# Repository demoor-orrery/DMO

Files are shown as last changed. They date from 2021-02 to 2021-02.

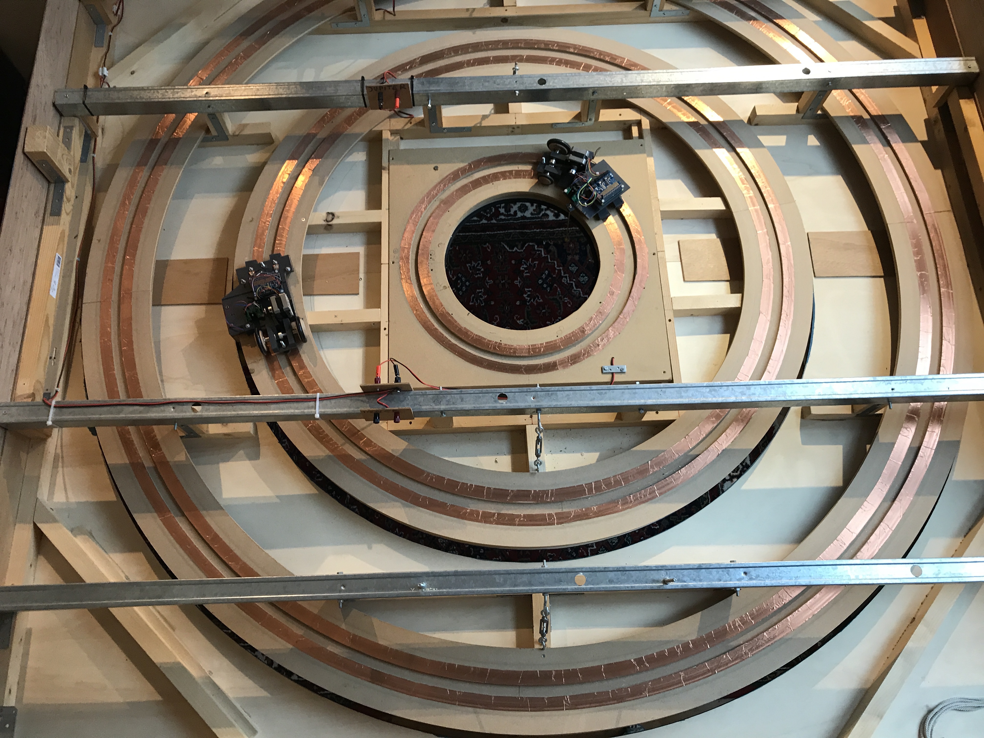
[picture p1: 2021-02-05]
pictures/DM005 frame overview without inner planets.JPG

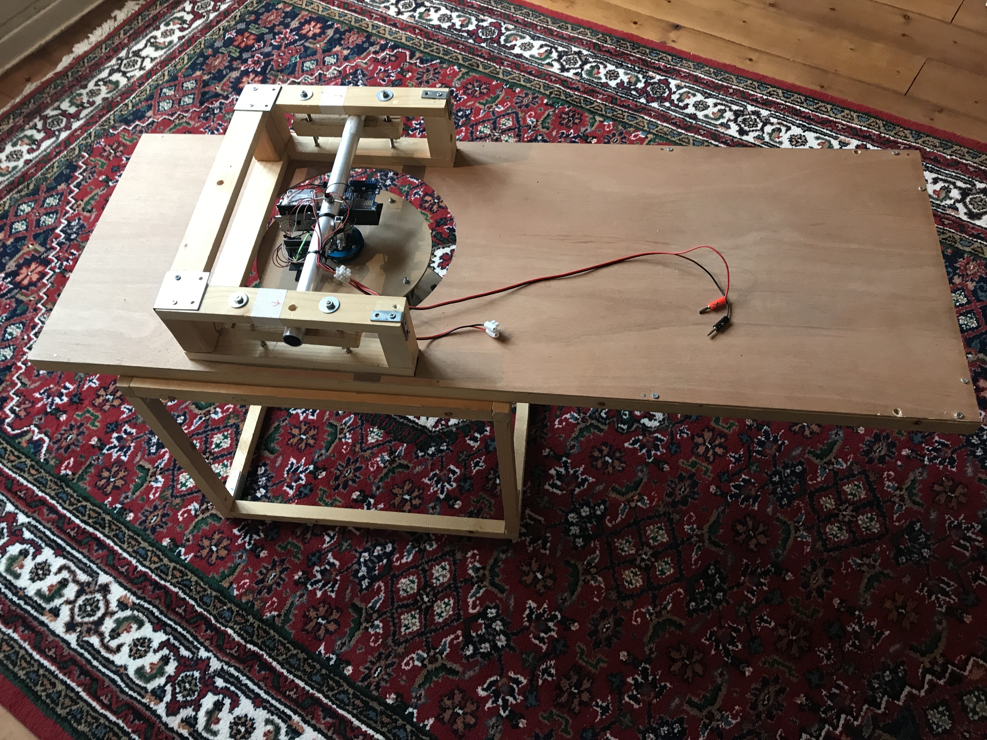
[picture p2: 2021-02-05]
pictures/DM007 inner system on floor.JPG

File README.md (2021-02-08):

# www.demoor-orrery.com/en

here all files are stored which will help to build your own planetrium

DMO.py <br>
the only file you need to run on your Pi

/documentation<br> 
please read them all before you start

/pictures<br>
all pictures used in documentation in full resolution for more details

/gerber file PCB<br>
files you need to print your own PCB board

/STL files for 3D <br>
all STL files for all components 

/webserver <br>
the adjusted JSOrrery software to run on your webserver for your DMO

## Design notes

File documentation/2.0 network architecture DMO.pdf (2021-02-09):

Tuesday, 9 February 2021

## 2.0 Network architecture DMO

2.1 Version control

Version 1.0 - 2 February 2021 - first version Version 1.1 - 9 February 2021 - typos fixed

2.2 Introduction

Each planet has its own computer (Raspberry Pi Zero W). A stepper motor (Nema
17) with accompanying driver (Adafruit Motor HAT) is connected so the planet can be exactly positioned. Initial positioning is done with reed-switches that react to magnets on the track.

The position of the planet is calculated on a website which is hosted on a webserver. Each planet can read the output via WiFi and calculate where its place is on the planet orbit for the entered date and then "drive" to it.

2.3 Architecture

webserver | the internet | DMO

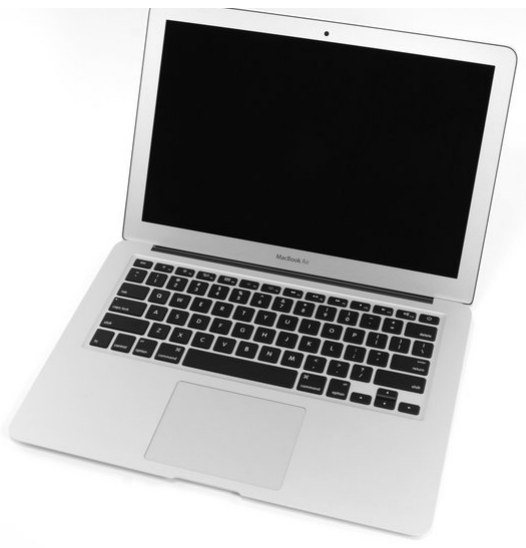
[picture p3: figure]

laptop, phone or tablet

1 | www.demoor-orrery.com/en

Tuesday, 9 February 2021
2.3.1 Webserver and software

The webserver can be any hosting-server, it is used to store the solar-systemsoftware. You can use any hosting-partner or set up one yourself in your network. As long as it runs the original JS Orrery software: http://mgvez.github.io/jsorrery/

Hosting it on an external server has the benefit you can operate the DMO outside your local premisses (anywhere in the world in fact).

The original JS Orrery software has been modified with adding a “save positions” button. What is basically does is sending out a string of degrees where the planets are on the entered date.

The string can be read at:

http://yourdomain.xxx/positions.txt

Example of possible output:

360185244155101132045097

The first three digits are for Mercury and so on (inside out until Pluto). The last three planets are not in the DMO but maybe in your DMO.

In our DMO Git account you will find the adjusted JS Orrery software you need to install on your webserver.

2.3.2 DMO

The DMO consist of 6 Raspberry Pi Zero W’s (RPI) which are all connected to the same local WiFi network. All planets (from Mercury to Saturn) “know” who they are and read their own part of the string for their position in their orbit.

2.3.3 Laptop, phone or tablet

With your terminal (doesn’t matter what it is as long as it runs a web-browser and supports Javascript) you can acces the webserver on your domain (http://yourdomain.xxx).

You enter the desired date, hit return and push “save positions”. The string is published and picked up by the relevant RPI’s. A RPI “knows” where it is via a reed switch which runs over a magnet, recalculates the degrees into number of steps and moves to the desired position.

2 | www.demoor-orrery.com/en

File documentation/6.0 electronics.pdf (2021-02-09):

Tuesday, 9 February 2021

## 6.0 Electronics

6.1 Version control

Version 1.0 - 2 February 2021 - first version Version 1.1 - 9 February 2021 - typos fixed

6.2 Introduction

This part of the documentation describes the electronics. That is the same for inner and outer planets. The basis consist of five parts: RPI, driver, stepper motor, power supply, reed switch

6.3 RPI

Not much to say here: you need a Raspberry Pi Zero W (or any other Pi with Wifi).

6.4 Driver

You need the Adafruit DC & Stepper Motor HAT for Raspberry Pi - Mini Kit. It comes along with a nice software library on which the DMO software is based.

6.5 Stepper motor

The NEMA17 is chosen for its availability, robustness and torque.

6.6 Power supply

The driver runs on 12V but the RPI on 5v, so the voltage must be decreased.

6.7 Reed switch

The RPI must now where it is. In order to do so there is one magnet sticked on every track. The RPI detects when the magnet is passed, sets its counter to zero and because he “knows” how many steps one round is he can determine how many steps the stepper should run to go to the right position.

1 | www.demoor-orrery.com/en

There is a problem with bouncing GPIO ports on an RPI. In order to prevent this you need the following solution:

6.8 Scheme and pcb

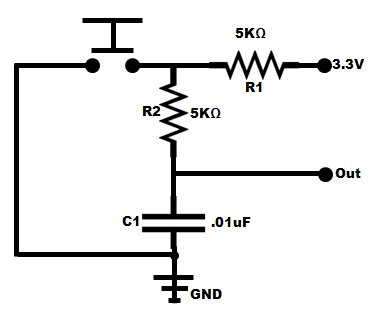
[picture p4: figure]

To integrate the solution for 6.6 and 6.7 a pcb board has been designed with this circuit.

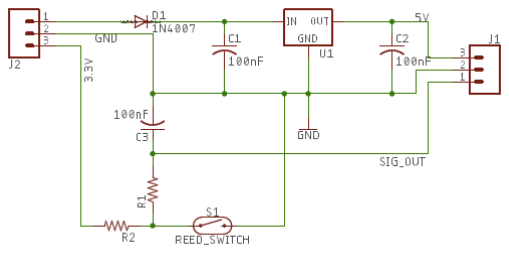
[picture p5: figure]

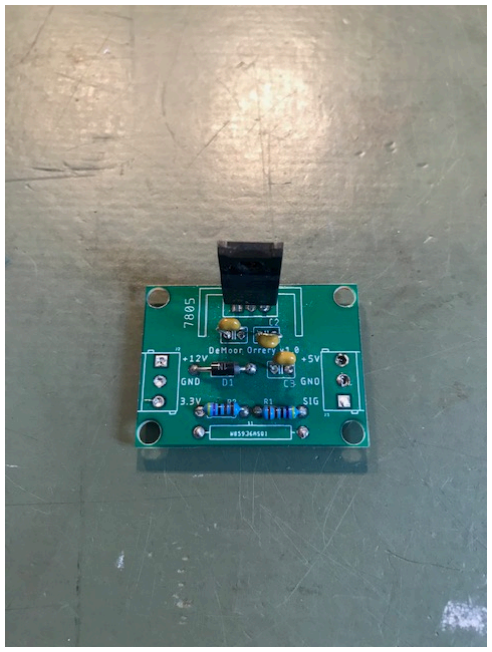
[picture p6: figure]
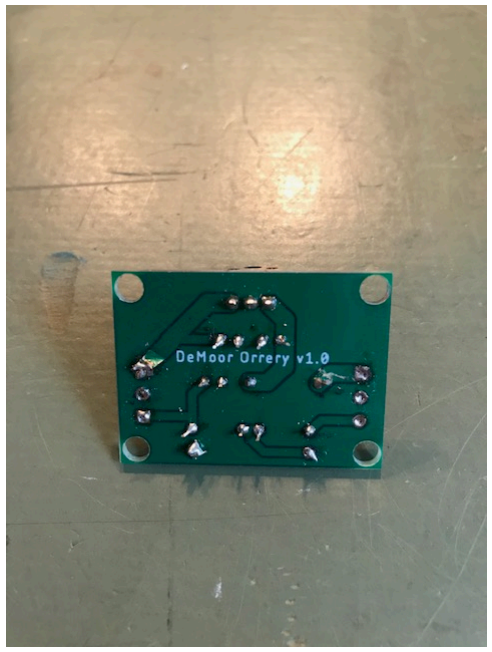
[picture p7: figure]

The accompanying gerber files are stored in our GIT account.

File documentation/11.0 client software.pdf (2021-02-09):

Tuesday, 9 February 2021

## 11.0 Client software

11.1 Version control

Version 1.0 - 2 February 2021 - first version Version 1.1 - 9 February 2021 - typos fixed

11.2 Introduction

This document describes the client software of the DMO.

11.3 Git

The client software can be found at https://github.com/demoor-orrery/DMO/

There is 1 file: DMO.py. Is has comments in the source to explain when needed.

You’ll need to install that on every RPI/planet.

11.4 General instructions

The software runs with python 3 and is pretty straight forward.

Make sure that every RPI has its correct hostname as that is how the RPI knows which planet it is.

Adafruit Motor HAT requires some special handling. Please read: https://learn.adafruit.com/adafruit-dc-and-stepper-motor-hat-for-raspberry-pi

DMO.py generates a log-file which is published at index.php. In order to read that during real time execution you will need to install the Apache webserver and PHP. Please read: https://www.raspberrypi.org/documentation/remote-access/webserver/apache.md (https://www.raspberrypi.org/documentation/remote-access/web-server/apache.md)

The RPI’s should have autoboot, meaning they start running DMO.py as soon as the power is switched on. In order to do so include the following line in /etc/rc.local

sudo nohup python3 -u /home/pi/DMO/DMO.py > /home/pi/DMO/DMO.log &

1 | www.demoor-orrery.com/en

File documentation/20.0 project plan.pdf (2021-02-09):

Tuesday, 9 February 2021

## 20.0 Project plan

20.1 Version control

Version 1.0 - 4 February 2021 - first version Version 1.1 - 9 February 2021 - typos fixed

20.2 Introduction

This global plan describes what steps to be taken in order to build your own DMO.

Step 1 Size

Define how big you want your DMO to be and how many planets you want to be serviced. Based on this decide what planet is an inner planet and what are outer planets.

Step 2 Set up and first planet

Set up your webserver and instal the JS Orrery scripts. Copy the client-software to your own GIT account and work from there.
Build the electronics for one planet (so 1 RPI, 1 driver etc.) in order to find out if you are comfortable enough to go all the way.
Step 3 Dimensioning the DMO

Make a detailed design for the frame.
Make a detailed design for the CNC cutter of all the (round) parts you need.
Step 4 Frame and winch

Do the CNC cutting (or find a company which will do it for you), make the frame. If you decide that you want to use a winch instead of manual hoisting do that before you make the frame.

Step 5 Inner system

Build the inner system.

1 | www.demoor-orrery.com/en

Tuesday, 9 February 2021
Step 6 Outer planets

Build the cars for the outer planets.

Step 7 Test and calibrate the DMO

As the magnets are randomly placed in the orbits you need to calibrate the system.

Step 8 Paint

If all works fine you can paint and place the graphics.

2 | www.demoor-orrery.com/en

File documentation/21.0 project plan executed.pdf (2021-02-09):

Tuesday, 9 February 2021

## 21.0 Project plan executed

20.1 Version control

Version 1.0 - 4 February 2021 - first version Version 1.1 - 9 February 2021 - typos fixed

20.2 Introduction

This document describes more in detail what I have done in step 1 to 8. You might go for a different solution so now and then.

Step 1 Size

Imagine (and measure) the outline of your DMO. Think about mounting points in your ceiling and where your 220 VAC is.

As my WiFi was rather crowded and RPI’s are not the best WiFi receivers I installed an extra router for the DMO.

If you are going to use a winch, think where it should be and how it is going to be fixed to the wall for example. Remember: the smallest DMO weighs more than 80 Kg, it better be safe.

Step 2 Set up and first planet

Set up your webserver and instal the JS Orrery scripts. Copy the client-software to your own GIT account and work from there.
Build the electronics for one planet (so 1 RPI, 1 driver etc.) in order to find out if you are comfortable enough to go all the way.

The local power supply and the reed switch stuff are a bunch of components (see the electric scheme). Somebody (again via fiverr.com) created a Printed Circuit Board file (a so called gerber file) for me which I send to PCBway.com. You can design one your own or use mine which is stored on Git.

TIP: order more then 6, they are cheap and you will probably mess up a few during this project.

1 | www.demoor-orrery.com/en

Step 3 Dimensioning the DMO

When you know how big your DMO is going to be it is time to measure. All the rings and dishes are related to each other.

I have made a spreadsheet in order to prevent miscalculations, see “80.0 DMO drawing example sheet”. The bigger (non darkened cels) can be filled in and the rest is calculated. The sheet is in Dutch for now. You should make your own spreadsheet for this.

Please note that the bigger circles have an A and a B, that is because of the maximum size of the CNC cutting table (and MDF sheets which are standard available). In total I needed 32 parts.

Most CNC machines work with DXF-files and you will need those in order to get your CNC-work done. Check your local CNC cutter first what kind of files he wants.

Once you are satisfied with the dimensioning make a drawing book, see “81.0 DMO drawing parts”, if you do not know how to get to a DXF-file. I have used fiverr.com to find a guy to do it for me for little money. He needs the book in order to fully understand what you want.

You can control his work by letting him generate a picture of the DXF-files. Example: “82.0 DMO dxf control file”.

When you have the DXF file you can go to your local CNC cutter and let them do the work.

Step 4 Frame and winch

Do the CNC cutting (or find a company which will do it for you), make the frame. If you decide that you want to use a winch instead of manual hoisting do that before you make the frame.

TIP: go for the winch! It is spectacular for your visitors but I did find out that it is really useful when you are working on your DMO because you have to lift it many times and it is a least 80 Kg’s.

Step 5 Inner system

Build the inner system. Halfway this project a bought myself a 3D printer: very useful for all special parts.

Step 6 Outer planets

Build the cars for the outer planets.

Step 7 Test and calibrate the DMO

As the magnets are randomly placed in the orbits you need to calibrate the system. You should make a few test-scripts in which the planets run for one round so you can count in how many steps a car (or dish) makes a round. You need these figures in the client software.

Step 8 Paint

If all works fine you can paint and place the graphics.

TIP: On the DMO are numbers for months, names of planets and Zodiac signs. If you do not have a steady hand you need another solution. I have somebody designed a set of stickers for this.

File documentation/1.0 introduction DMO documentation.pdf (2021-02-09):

Tuesday, 9 February 2021

## 1.0 Introduction DMO documentation

1.1 Version control

Version 1.0 - 2 February 2021 - first version
Version 1.1 - 9 February 2021 - added paragraph 1.3, extended 1.4

1.2 Introduction

An orrery or planetarium is a scale model from our solar system. An orrery was in the past a mechanical model with radars, clocks and chains, nowadays they are mostly virtual with lasers projecting the planets and stars at a ceiling.

A DMO (DeMoor-Orrery) is an electromechanical planetarium that was created after an inspirational visit to the planetarium of Eise Eisinga.

This document is part of a set of documents which describe the DMO as shown on https://www.demoor-orrery.com/en in order to build one yourself.

All pictures used in this documentation are stored on Github in high resolution to browse for more detail.

1.3 Skill set required

This documentation is not a detailed construction manual. It assumes you have the following skill sets:
- medior knowledge of woodworking and construction in general
- medior knowledge of programming and Raspberry Pi
- basic knowledge of hosting
- basic knowledge and experience with 3D printing
- basic knowledge of astronomy

1.4 Right of use and liability

Anyone is free to copy, modify, publish, use, compile, sell, or distribute all files of the DMO including its documentation, either in source code form or as a compiled binary, for any purpose, commercial or non-commercial, and by any means.

All files are provided “as is”, without warranty of any kind, express or implied. In no event shall the author be liable for any claim, damages or other liability.

1 | www.demoor-orrery.com/en

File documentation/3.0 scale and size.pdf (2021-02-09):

Tuesday, 9 February 2021

## 3.0 Scale and size

3.1 Version control

Version 1.0 - 2 February 2021 - first version Version 1.1 - 9 February 2021 - typos fixed

3.2 Introduction

How big is your DMO going to be and which planets have to be serviced.

3.3 Frame size

This is the first question: what part of the ceiling you want to use for the planetarium and how big is it?

The DMO on https://www.demoor-orrery.com/en is 2,20 x 2,20 meter and runs the first 6 planets.

How many square-space do you have available?

How are you going to mount it to the ceiling?

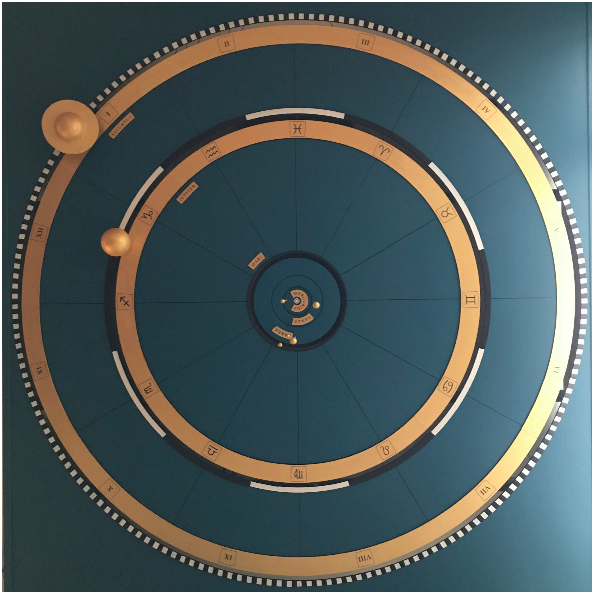
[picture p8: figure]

3.4 Orbit scale

Once you have determined what the surface is you can determine how many orbits (the circle in which the planet moves) you can depict on your DMO.

There are all kinds of calculation tools to be found on the internet. An easy to use example can be found at: https://thinkzone.wlonk.com/SS/SolarSystemModel.php

The measurements of the example DMO are depicted in the next table. The numbers are the rays from the Sun to the planet in Astronomical Units (real distance) and in centimeters (DMO distance). Conclusion: with a 2,20 x 2,20 DMO you can fit the first 6 planets from our solar system. If you have a bigger DMO you can fit more planets. The software serves all 9 planets, it is all a matter of physical space.

1 | www.demoor-orrery.com/en

Note: in real life the orbits are not concentric circles, have a look at Eise Eisinga’s planetarium. But to reduce the complexity of this planetarium they are.

3.5 Two scales

This is somewhat confusing. There are two scales in a DMO. The first scale is the distance between the planets, the other scale is the size of the planets.

If you want to size your planets in your DMO on the same scale as the distance you need an incredible big DMO. To have a thorough understanding of what I’m saying: please have a look at: https://vimeo.com/139407849. A beautiful made video from a group of friends who made a model in the desert. Gives you a good sense of how big our solar system is or how small we are on our own planet.

planet | distance to Sun in AU | distance to Sun in cm | remark
Mercury | 0,39 | 4,26
Venus | 0,72 | 7,96
Earth | 1 | 11
Mars | 1,52 | 16,76
Jupiter | 5,2 | 57,23
Saturn | 9,57 | 105,27
Uranus | 19,3 | 212,33 | not in this DMO
Neptunes | 30,27 | 332,98 | not in this DMO
Pluto | 39,61 | 435,73 | not in this DMO

3.6 Planet scales

So use a different scale for the planets. Have a look at what looks good in the DMO. You can use https://thinkzone.wlonk.com/SS/SolarSystemModel.php for actual planet scaling as well.

Next to this all we have Jupiter and Saturn: they are rather big compared to the rest. I doesn’t look that smooth two have 2 giant soccer balls in your carefully designed planetarium.

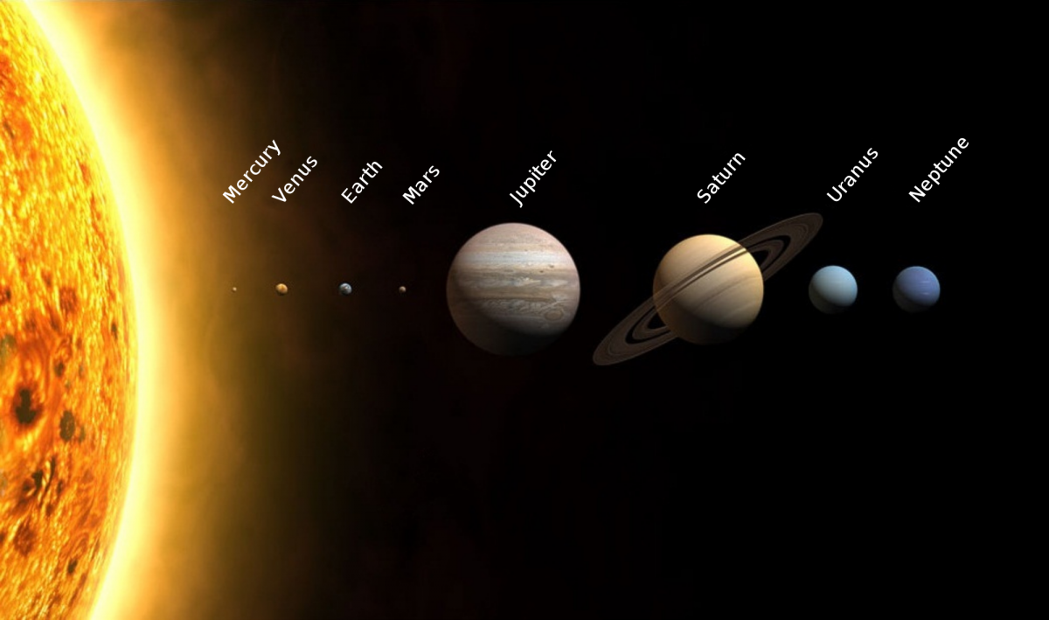
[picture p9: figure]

There is no mathematical solution for this. Just make them smaller. For your comfort: Eise Eisinga did it as wel in 1786.

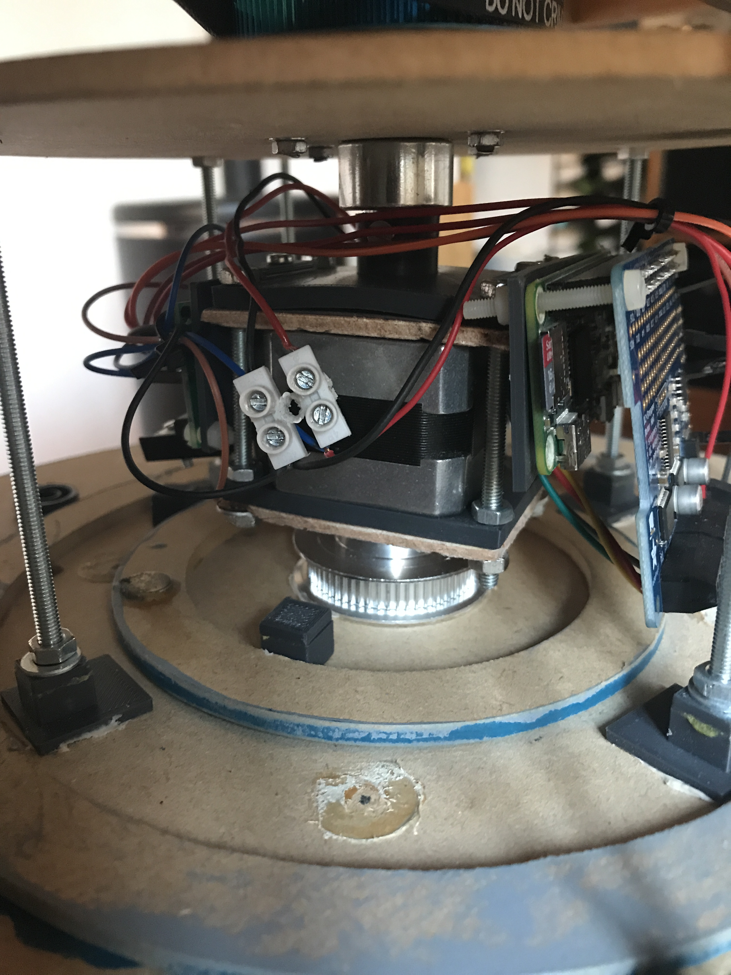
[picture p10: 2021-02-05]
pictures/DM017 mercury.JPG

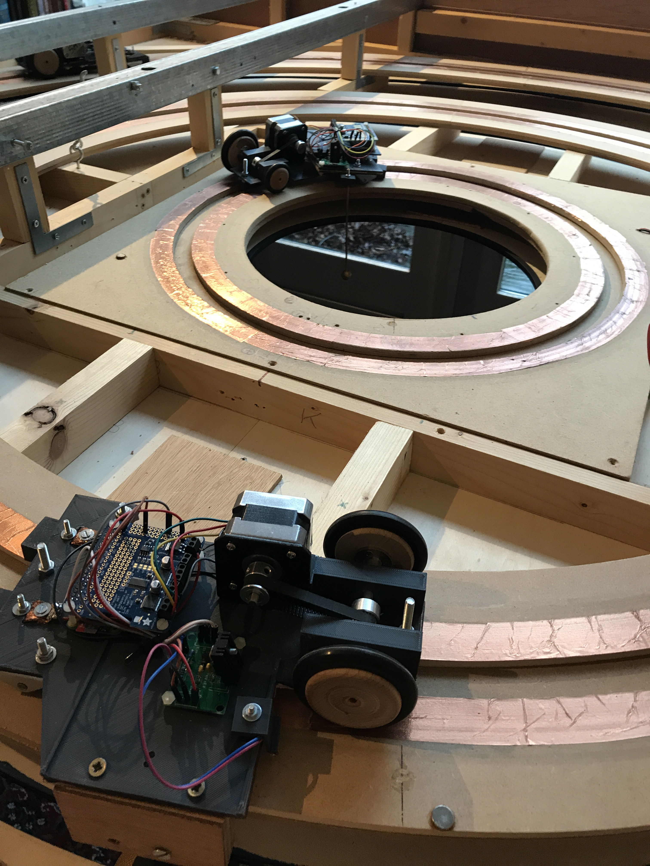
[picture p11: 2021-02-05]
pictures/DM004 closeup inner planets out of frame.JPG

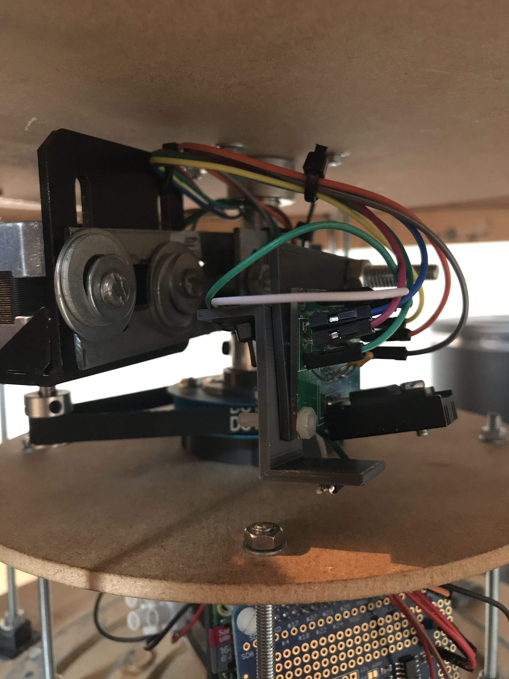
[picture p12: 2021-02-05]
pictures/DM014 venus.JPG

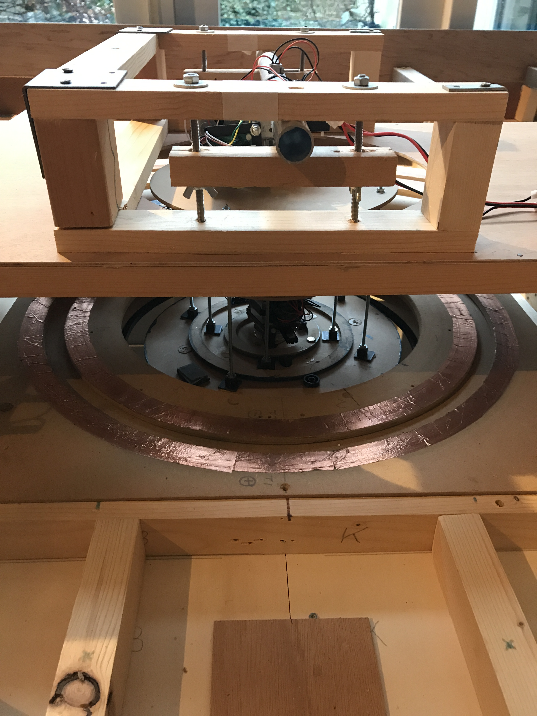
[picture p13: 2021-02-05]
pictures/DM002 inner planets in frame.JPG

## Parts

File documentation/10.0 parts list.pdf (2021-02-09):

Tuesday, 9 February 2021

## 10.0 Parts list

10.1 Version control

Version 1.0 - 2 February 2021 - first version Version 1.1 - 9 February 2021 - typos fixed

10.2 Introduction

This is the parts list of all critical components. Resistors, capacitors, wires, mounting brackets, nuts and bolts et cetera are not detailed for now.

10.3 Electronics

This is for all 6 planets the same:

10.4 Frame

1 | www.demoor-orrery.com/en
raspberry pi | 6 | RPI Zero W, any type will do as long as it has WiFi
motor HAT | 6 | Adafruit DC & Stepper Motor HAT for Raspberry Pi - Mini Kit
40 pin male header | 6 | to mount the HAT to the RPI
SD kaart 16 gig | 6 | preferably industrial grade
motor HAT | 6 | NEMA17
local power supply | 6 | L7805CP, 1.5 A
local reed switch | 6 | preferably in plastic case because switches are vulnerable as they are made from glass
magnets | 6 | small and flat
GT2 pulley | 6 | to mount to NEMA17
power supply 12V 10A | 1 | 220 VAC input, 12VDC 10 A output
copper tape | 1 | CFT-25/33M copper tape CFT25 (l x b) 33 m x 25 mm 33 meter

Tuesday, 9 February 2021
10.5 Outer planets

10.6 Inner planets

10.7 Other materials

Furthermore: you need to think with what material you want to build your frame, lightning of the DMO if needed, paint, graphics etc.

You lift your DMO manually or do you have otherwise access? If you need a winch you have to figure out that construction as well.

10.8 Costs

The DMO as pictured on the website has roughly about 4500 euro of materials and services (mostly CNC cutting of the orbits) in it.

That is if you do not brake anything along the project….

2 | www.demoor-orrery.com/en
copper wire | 1 | Kabeltronik copper wire woven band, 1 meter will do
GT2 belt | 3 | mars, jupiter and saturn
set of 1 axle and 2 front wheels and pulley | 3 | any wheel will do
set of 2 rear wheels | 3 | any wheel will do
GT2 belt | 2 | earth and venus
GT2 pulley | 2 | to propel the dish

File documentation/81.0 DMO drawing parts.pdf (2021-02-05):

## Maten zaagwerk Planetarium Deel 1

Plafond, Saturnus en Jupiter

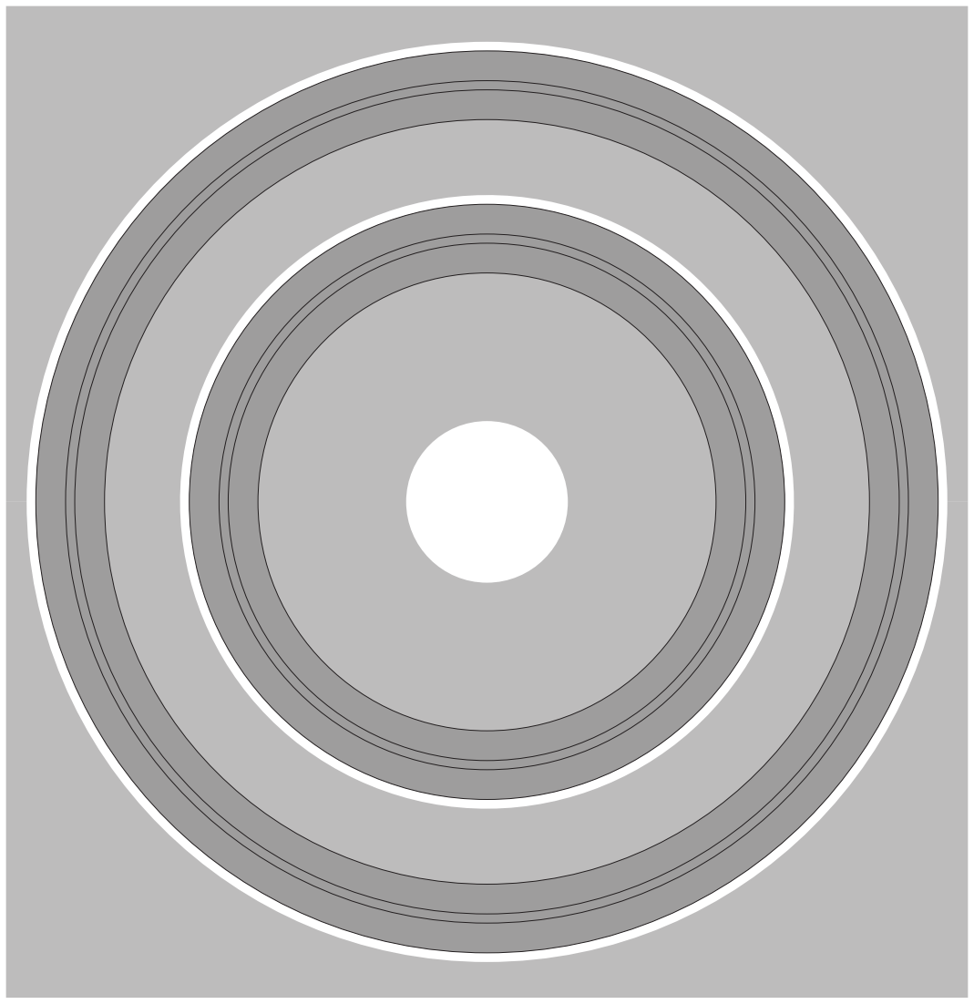
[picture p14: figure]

Datum: 07/08/2018

Plafond buitenkant A

Nummer: 1

210 cm

201 cm

108,30 cm

100,50 cm

Datum: 07/08/2018

Plafond tussenring A

Nummer: 2

197 cm

134 cm

Datum: 07/08/2018

Plafond binnenring A

Nummer: 3

130 cm

35,30 cm

Datum: 07/08/2018

Plafond buitenkant B

Nummer: 4

210 cm

201 cm

108,30 cm

100,50 cm

Datum: 07/08/2018

Plafond tussenring B

Nummer: 5

197 cm

134 cm

Datum: 07/08/2018

Plafond binnenring B

Nummer: 6

130 cm

35,30 cm

Datum: 07/08/2018

Saturnusbaan A

Nummer: 7

197 cm

167 cm

Datum: 07/08/2018

Saturnusrail binnen A

Nummer: 8

180 cm

167 cm

Datum: 07/08/2018

Saturnusrail buiten A

Nummer: 9

197 cm

184 cm

Datum: 07/08/2018

Saturnusbaan B

Nummer: 10

197 cm

167 cm

Datum: 07/08/2018

Saturnusrail binnen B

Nummer: 11

180 cm

167 cm

Datum: 07/08/2018

Saturnusrail buiten B

Nummer: 12

197 cm

184 cm

Datum: 07/08/2018

Jupiterbaan A

Nummer: 13

130 cm

100 cm

Datum: 07/08/2018

Jupiterrail binnen A

Nummer: 14

113 cm

100 cm

Datum: 07/08/2018

Jupiterrail buiten A

Nummer: 15

130 cm

117 cm

Datum: 07/08/2018

Jupiterbaan B

Nummer: 16

130 cm

100 cm

Datum: 07/08/2018

Jupiterrail binnen B

Nummer: 17

113 cm

100 cm

Datum: 07/08/2018

Jupiterrail buiten B

Nummer: 18

130 cm

117 cm

## Maten zaagwerk Planetarium Deel 2

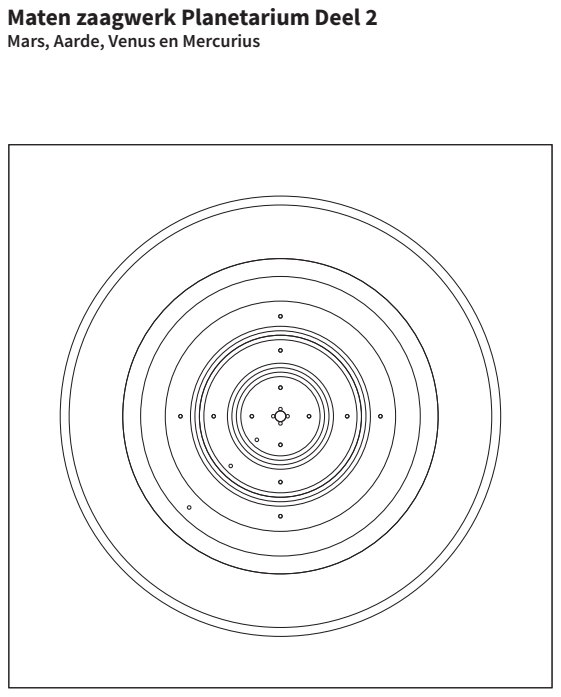
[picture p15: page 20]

Mars, Aarde, Venus en Mercurius

Deel 2
Mars, Aarde, Venus
en Mercurius
Datum: 06/08/2018

Datum: 07/08/2018

Mars baan

Nummer : 19

35,30 cm
60,8 cm

60,8 cm

Datum: 07/08/2018

Marsrail binnen

Nummer : 20

47,30 cm
35,30 cm

Datum: 07/08/2018

Marsrail buiten

Nummer : 21

49,30 cm

60,8 cm

60,8 cm

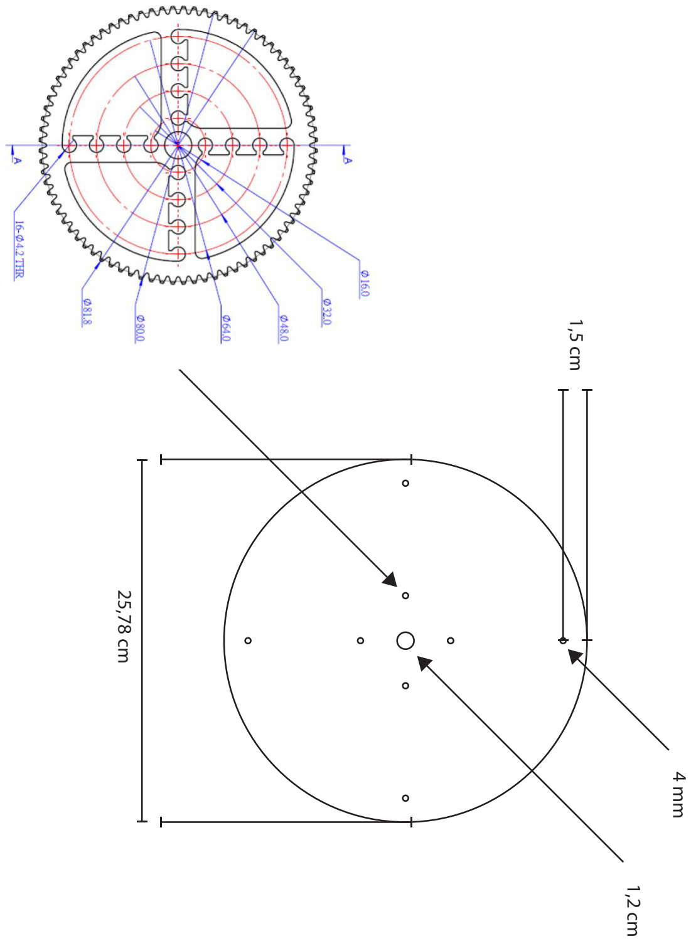
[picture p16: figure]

Datum: 07/08/2018

Aarde draaiplateau

Nummer : 22

Datum: 07/08/2018

Aarde zicht-ring

Nummer : 23

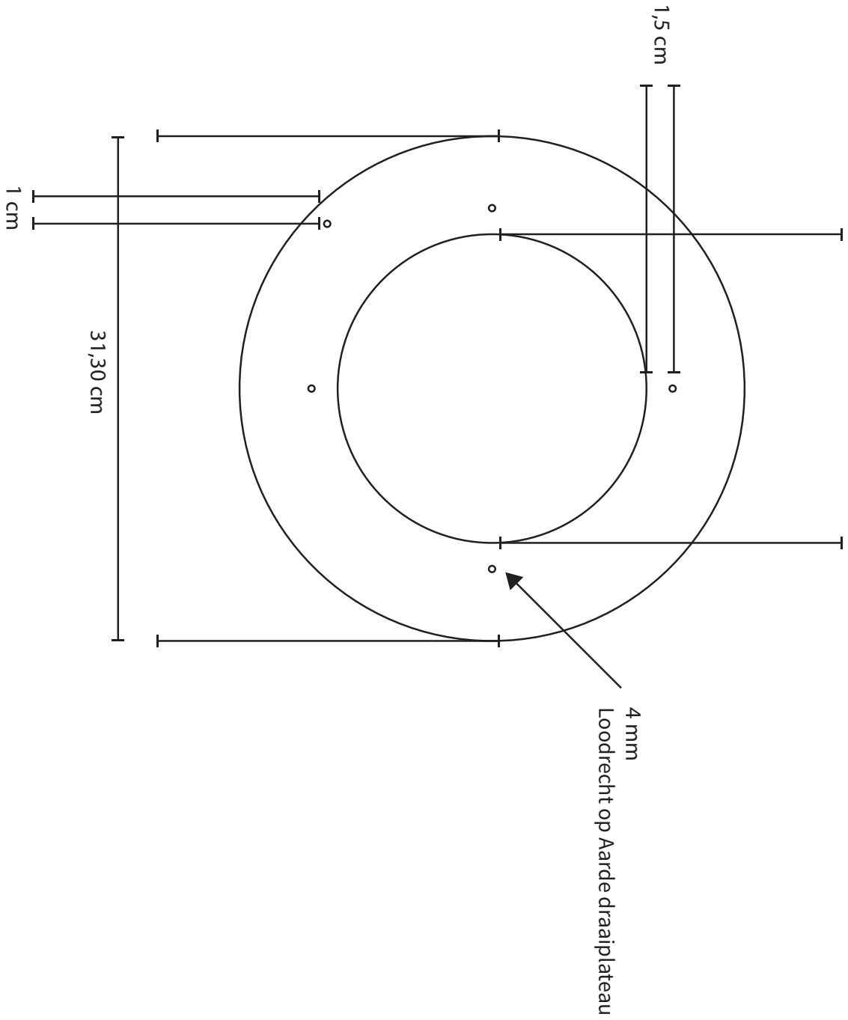
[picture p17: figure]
Loodrecht op Aarde draaiplateau

19,14 cm

Datum: 07/08/2018

Aarde dek-ring

Nummer : 24

20,14 cm

17,14 cm

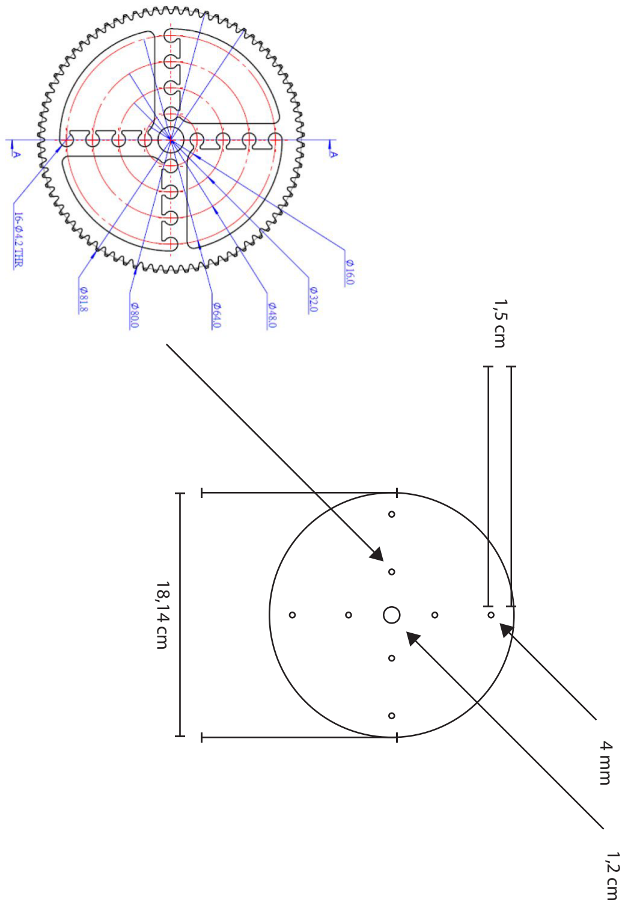
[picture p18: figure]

Datum: 07/08/2018

Venus draaiplateau
Nummer : 25

Datum: 07/08/2018

Venus zicht-ring

Nummer : 26

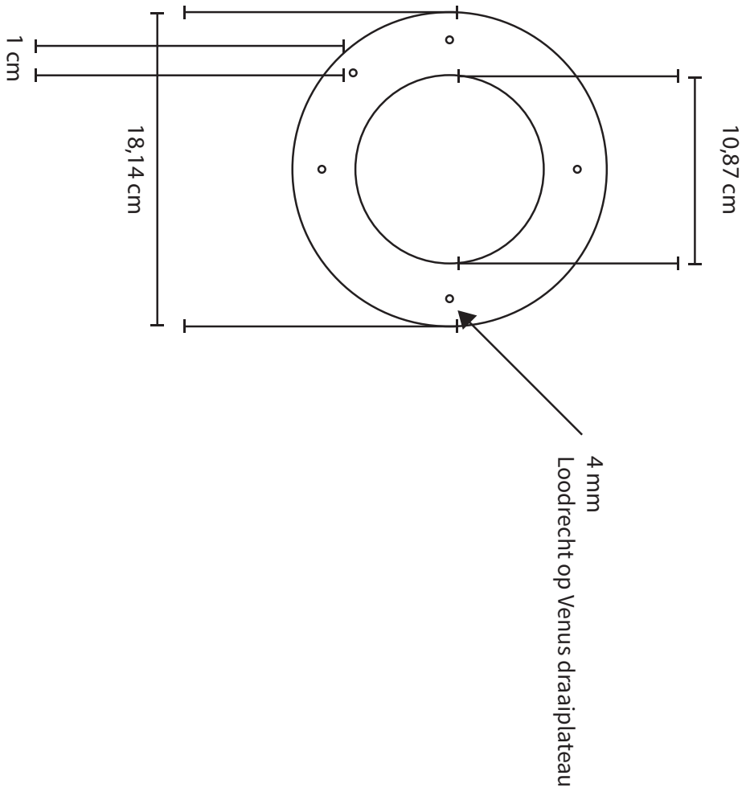
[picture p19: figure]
Loodrecht op Venus draaiplateau

Datum: 07/08/2018

Venus dek-ring

Nummer : 27

11,87 cm
8,87 cm

Datum: 07/08/2018

Mercurius draaiplateau/zicht-ring

Nummer : 28

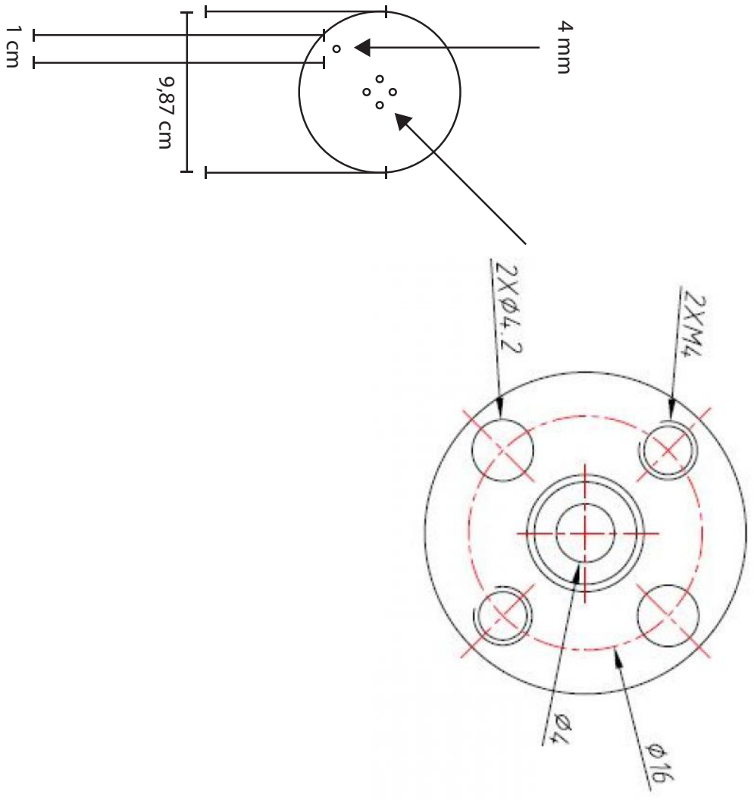
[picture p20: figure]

Datum: 07/08/2018

Losse ring

Nummer : 29

7 cm

4 mm

Datum: 07/08/2018

Losse ring

Nummer : 30

7 cm

4 mm

Datum: 07/08/2018

Losse ring

Nummer : 31

7 cm

4 mm

Datum: 07/08/2018

Ring om saturnus

Nummer : 32

45,08 cm

25,08 cm

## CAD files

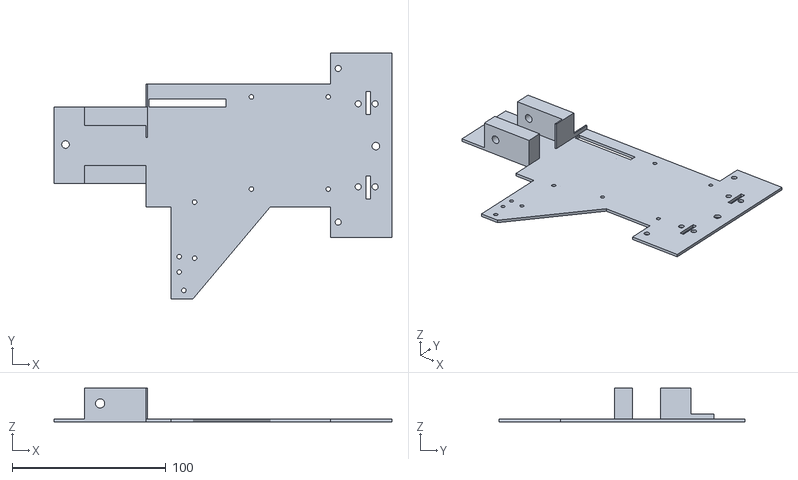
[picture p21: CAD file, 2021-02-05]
STL files for 3D printing/002 buitenkar Mars.stl
220.0 x 160.0 x 22.0

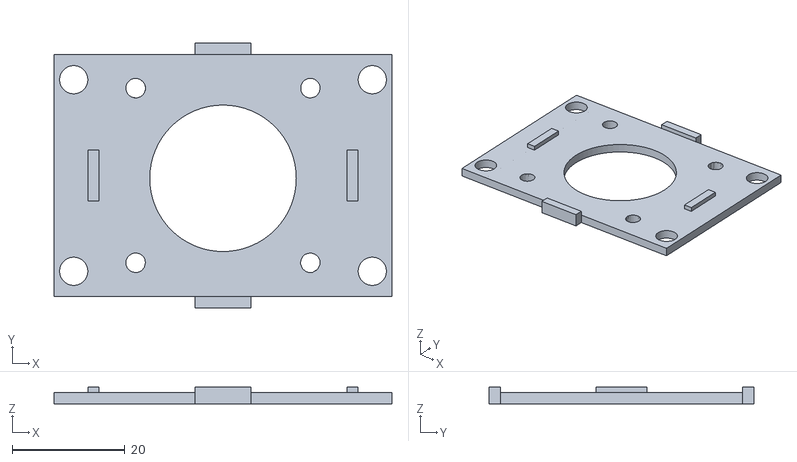
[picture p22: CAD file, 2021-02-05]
STL files for 3D printing/029 onderkant nema17 mercurius.stl
60.0 x 47.0 x 3.00

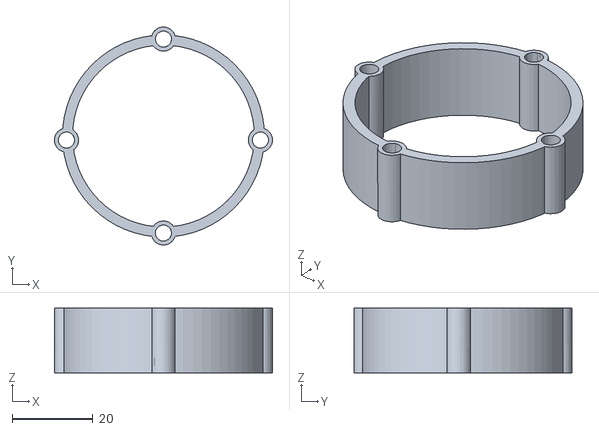
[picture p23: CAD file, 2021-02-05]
STL files for 3D printing/011 afstandhouder wiel op plateau 16mm.stl
54.0 x 54.0 x 16.0

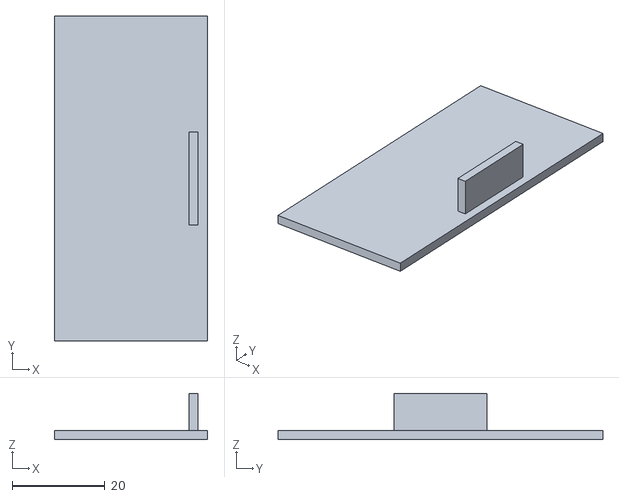
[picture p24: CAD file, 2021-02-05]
STL files for 3D printing/032 RPI nema17 mercurius.stl
33.0 x 70.0 x 10.0

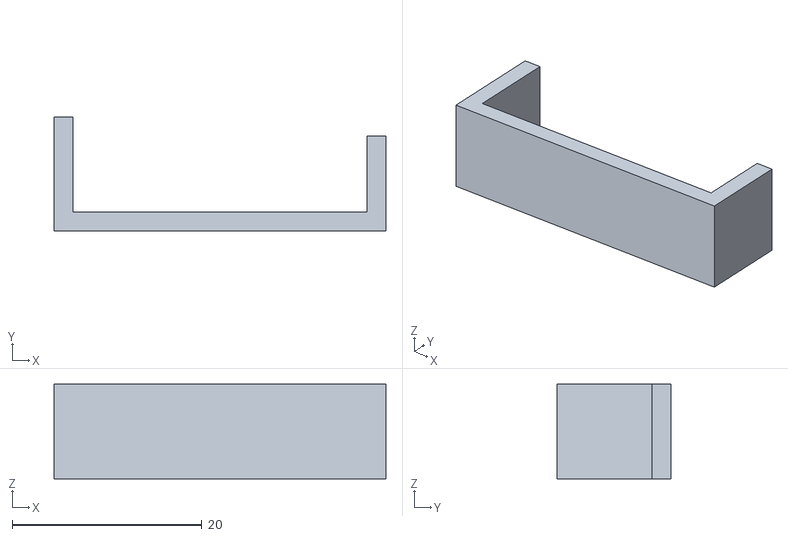
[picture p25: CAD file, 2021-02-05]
STL files for 3D printing/015 reedhouder Mercurius.stl
35.0 x 12.0 x 10.0

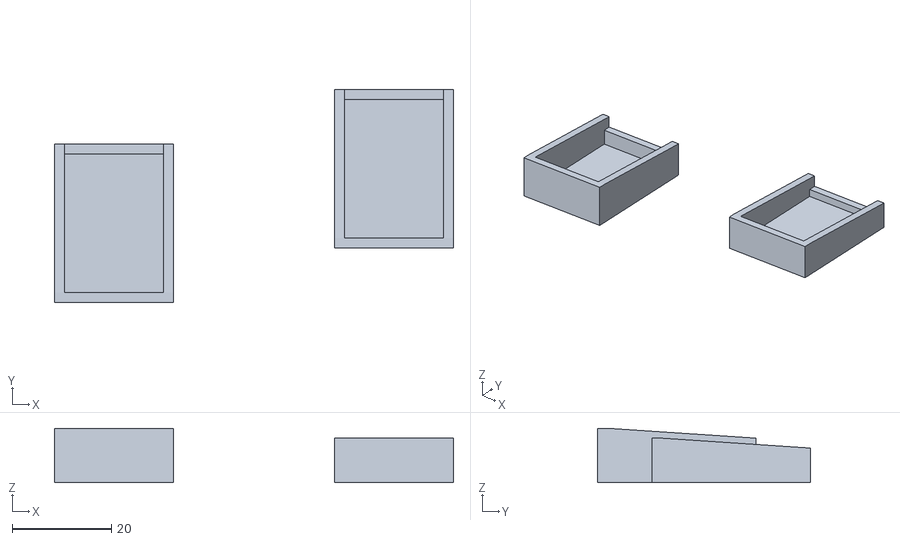
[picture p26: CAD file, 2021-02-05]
STL files for 3D printing/019 sleepcontact mars.stl
80.5 x 43.0 x 11.0

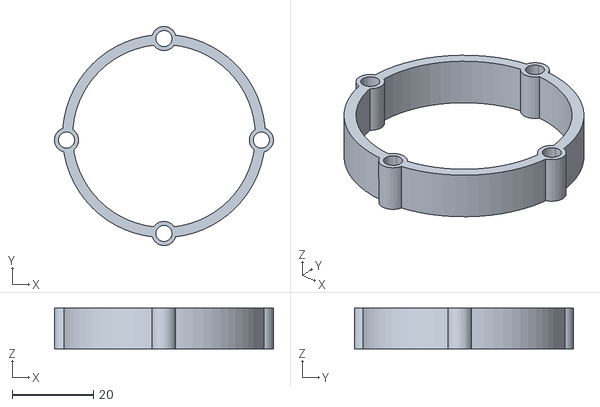
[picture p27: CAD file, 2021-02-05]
STL files for 3D printing/024 afstandhouder wiel op plateau 10mm.stl
53.9 x 54.0 x 10.00

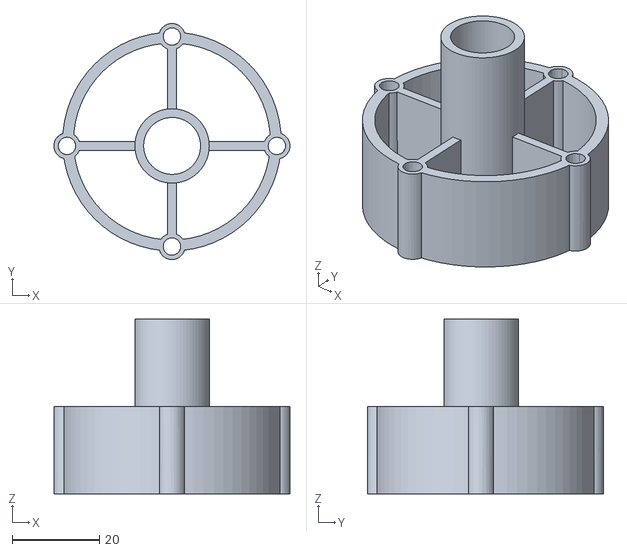
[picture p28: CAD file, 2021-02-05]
STL files for 3D printing/010 afstandhouder wiel op plateau 20 mm.stl
54.0 x 54.0 x 40.0

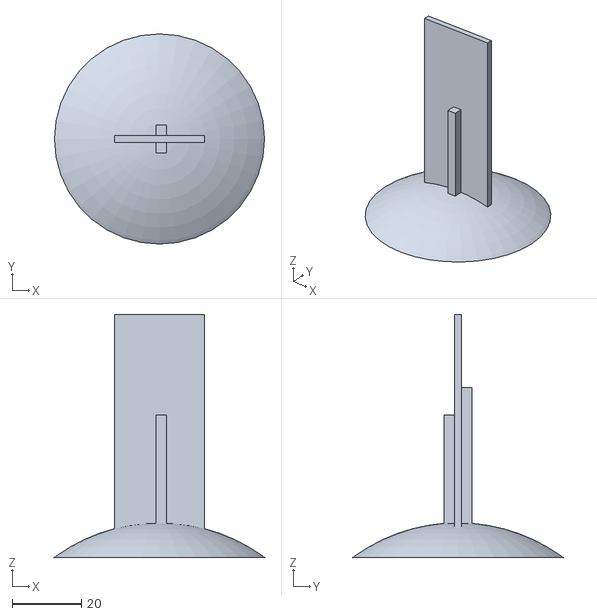
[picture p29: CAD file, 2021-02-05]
STL files for 3D printing/033 bolhouder.stl
60.5 x 60.5 x 70.0

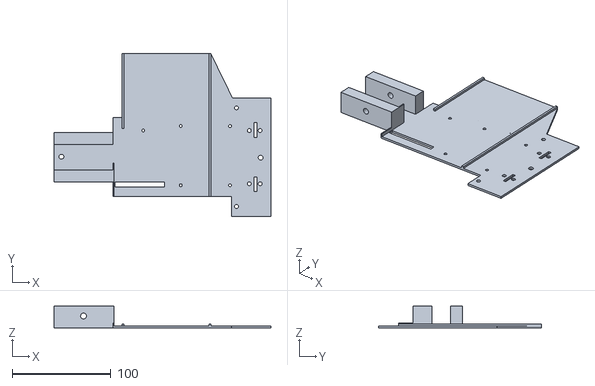
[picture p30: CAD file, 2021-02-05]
STL files for 3D printing/001 buitenkar SatJup versie2.stl
220.0 x 165.0 x 22.0

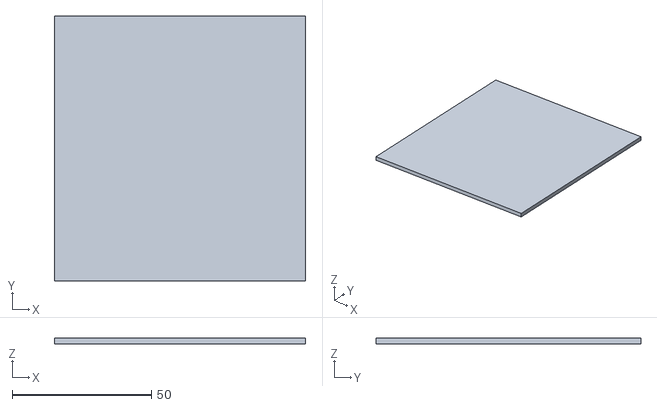
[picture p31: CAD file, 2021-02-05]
STL files for 3D printing/027 elektronicahouder mars.stl
90.0 x 95.0 x 2.00

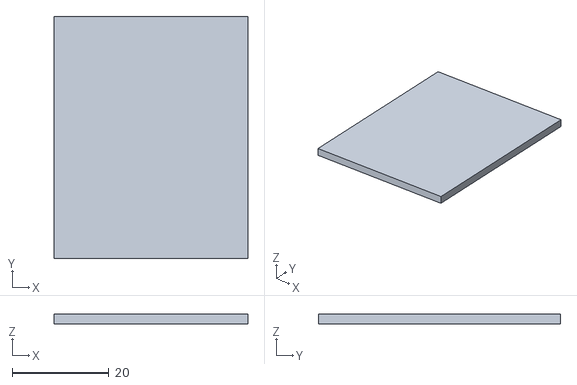
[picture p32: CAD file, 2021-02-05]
STL files for 3D printing/026 voedinghouder venus aarde.stl
40.0 x 50.0 x 2.00

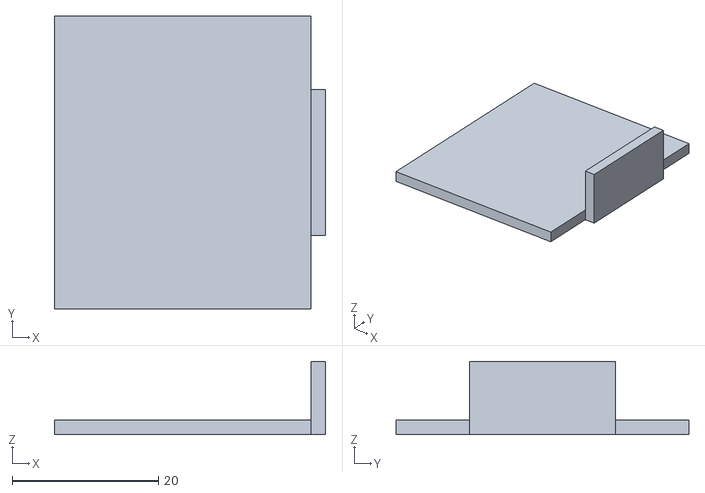
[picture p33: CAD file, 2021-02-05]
STL files for 3D printing/031 voeding nema17 mercurius.stl
37.0 x 40.0 x 10.0

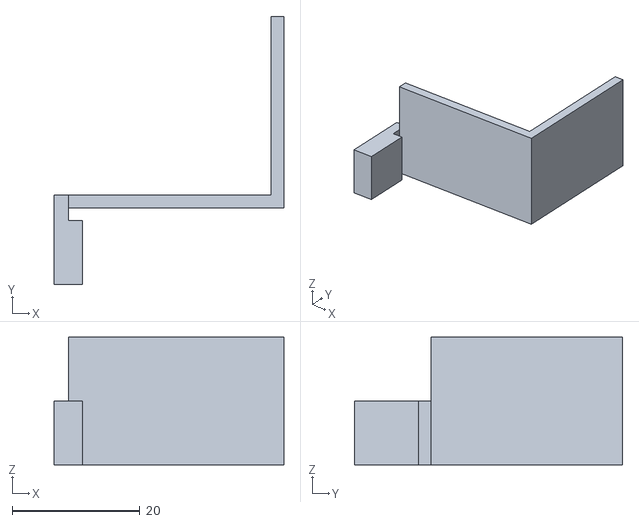
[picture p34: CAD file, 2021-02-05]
STL files for 3D printing/013 reedhouder Aarde.stl
36.0 x 42.0 x 20.0

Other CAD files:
STL files for 3D printing/017 M4 ringhouder.stl
STL files for 3D printing/025 RPIhouder venus aarde.stl
STL files for 3D printing/008 afstandring hoog.stl
STL files for 3D printing/021 sleepcontact sat jup.stl
STL files for 3D printing/007 afstandring laag.stl
STL files for 3D printing/009 planeethouders M3.stl
STL files for 3D printing/012 reedhouder Venus versie2.stl
STL files for 3D printing/020 reedhouder mars.stl
STL files for 3D printing/022 reedhouder sat jup.stl
STL files for 3D printing/023 planeethouder mars.stl
STL files for 3D printing/030 bovenkant nema17 mercurius.stl

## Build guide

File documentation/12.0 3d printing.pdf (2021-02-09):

### Tuesday, 9 February 2021

# 12.0 3d printing

## 12.1 Version control

### Version 1.0 - 7 February 2021 - first version Version 1.1 - 9 February 2021 - typos fixed

## 12.2 Introduction

### This document describes the published STL-files. Files made with Tinkercad. All

files printend in PLA filament.

The filenames are in Dutch, English translation in paragraph 12.3.

1 | www.demoor-orrery.com/en

### Tuesday, 9 February 2021

## 12.3 Files

2 | www.demoor-orrery.com/en
filename | remarks
001 buitenkar SatJup.stl | base plate Saturn Jupiter car
002 buitenkar Mars.stl | base plate Mars
007 afstandring laag.stl | spacer
008 afstandring hoog.stl | spacer
009 planeethouders M3.stl | mounting planet rod
010 afstandhouder wiel op plateau 20 mm.stl | GT2 mounting bracket
011 afstandhouder wiel op plateau 16mm.stl | GT2 mounting bracket
012 reedhouder Venus versie2.stl | switch holder Venus
013 reedhouder Aarde.stl | switch holder Earth
015 reedhouder Mercurius.stl | switch holder Mercury
017 M4 ringhouder.stl | for connecting visible dish Earth, Venus to propelling dish with M4 rod
019 sleepcontact mars.stl | contacts copper wire holder
020 reedhouder mars.stl | switch holder Mars
021 sleepcontact sat jup.stl | contacts copper wire holder
022 reedhouder sat jup.stl | switch holder
023 planeethouder mars.stl | planet holder Mars
024 afstandhouder wiel op plateau 10mm.stl | spacer
025 RPIhouder venus aarde.stl | mounting RPI Venus Earth
026 voedinghouder venus aarde.stl | mounting power supply Venus Earth
027 elektronicahouder mars.stl | electronics Mars
029 onderkant nema17 mercurius.stl | mounting bracket Mercury
030 bovenkant nema17 mercurius.stl | mounting bracket Mercury
031 voeding nema17 mercurius.stl | mounting bracket Mercury
032 RPI nema17 mercurius.stl | mounting bracket Mercury
033 bolhouder.stl | mounting bracket Saturn Jupiter sphere

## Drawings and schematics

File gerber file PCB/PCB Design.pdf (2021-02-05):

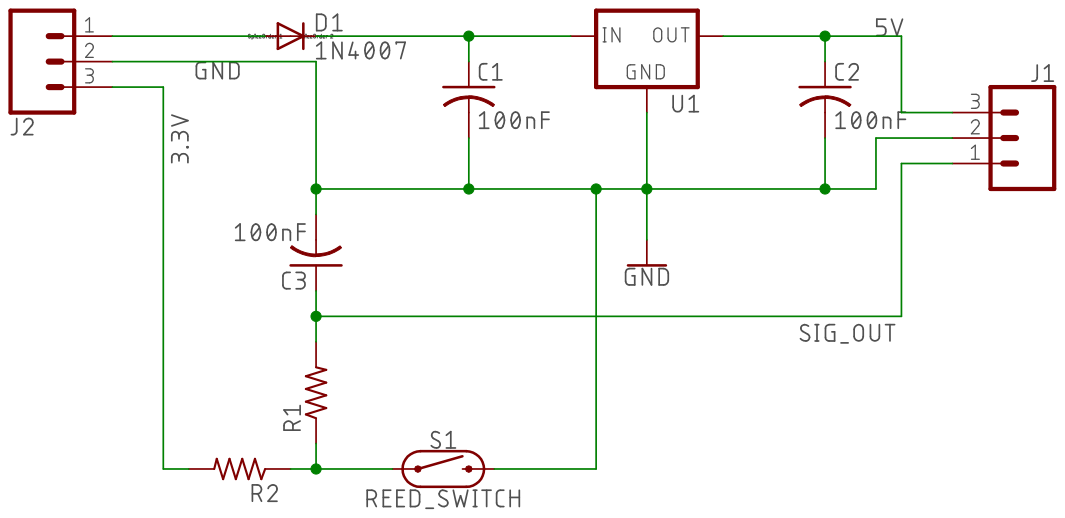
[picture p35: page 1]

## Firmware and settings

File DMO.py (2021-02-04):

import socket
import requests
from datetime import datetime
from time import sleep
import os
import wiringpi
from adafruit_motorkit import MotorKit
from adafruit_motor import stepper

# string from webserver
url = 'http://yourdomain.xxx/positions.txt'

# this is for testing, leave it as is
test_modus = False
planeet_motor = True
if test_modus:
   url = 'http://192.168.178.52/positions.txt'

# which planet are we?
planeet = socket.gethostname()

if (planeet == "DMO-Saturnus"):
   totaal_stappen = 6683 # number of steps to make one full circle, 1% deviation
   magneet_positie = 2  # position in degrees where the magnet of the planet is
   beginpos_string = 15  # de beginpositie in de string bij de Curl van deze planeet
   eindpos_string  = 18  # de eindpositie in de string bij de Curl van deze planeet
   richting = stepper.BACKWARD
   stijl = stepper.DOUBLE
if (planeet == "DMO-Jupiter"):
   totaal_stappen = 4326 # number of steps to make one full circle, 1% deviation
   magneet_positie = 5  # position in degrees where the magnet of the planet is
   beginpos_string = 12  # de beginpositie in de string bij de Curl van deze planeet
   eindpos_string  = 15  # de eindpositie in de string bij de Curl van deze planeet
   richting = stepper.BACKWARD
   stijl = stepper.DOUBLE
if (planeet == "DMO-Mars"):
   totaal_stappen = 2045 # number of steps to make one full circle, 1% deviation
   magneet_positie = 88  # position in degrees where the magnet of the planet is
   beginpos_string = 9  # beginposition in the string 
   eindpos_string  = 12  # endposition in the string 
   richting = stepper.FORWARD
   stijl = stepper.DOUBLE
if (planeet == "DMO-Aarde"):
   totaal_stappen = 1107 # number of steps to make one full circle, 1% deviation
   magneet_positie = 106   # 6 september, position in degrees where the magnet of the planet is
   beginpos_string = 6  # beginposition in the string 
   eindpos_string  = 9  # endposition in the string 
   richting = stepper.BACKWARD
   stijl = stepper.DOUBLE
if (planeet == "DMO-Venus"):
   totaal_stappen = 1019 # aantal stappen om een rondje te maken, 1% afwijking per keer
   magneet_positie = 281  # position in degrees where the magnet of the planet is
   beginpos_string = 3  # beginposition in the string 
   eindpos_string  = 6  # endposition in the string 
   richting = stepper.BACKWARD
   stijl = stepper.DOUBLE
if (planeet == "DMO-Mercurius"):
   totaal_stappen = 202 # aantal stappen om een rondje te maken, 1% afwijking per keer
   magneet_positie = 83   # position in degrees where the magnet of the planet is
   beginpos_string = 0  # beginposition in the string 
   eindpos_string  = 3  # endposition in the string 
   richting = stepper.BACKWARD
   stijl = stepper.DOUBLE
    
# reedswitch
os.system('gpio export 19 in')
sleep(0.5)
io = wiringpi.GPIO(wiringpi.GPIO.WPI_MODE_GPIO_SYS)
io.pinMode(19,io.INPUT)

# Adafruit
kit = MotorKit()

schakelaar = "open"
teller = 1
positiestring     = ""
positiestring_oud = "001001001001001001001001001"
totaalteller = 1
offline_teller = 1

# first time startup wait 30 seconds for all background processes of RPI to startup, prevents bumpy ride in the beginning
sleep (30)

while True:

  #timestamp  DMO.log
  now = datetime.now()
  dt_string = now.strftime("%d/%m/%Y %H:%M:%S")
  print ('-------------------------------')
  print (totaalteller , ' ' + dt_string + ' ' + planeet)
  
  try:
       r = requests.get(url, timeout=4)
       positiestring = r.text
       print ('ONLINE')
       offline_teller = 1
  except requests.exceptions.ConnectionError:
       positiestring = positiestring_oud
       print ('OFFLINE ', offline_teller)
       offline_teller +=1
       if offline_teller > 10:
          print ('RESTART ' + dt_string)
          os.system('sudo cp /home/pi/DMO/DMO.log /home/pi/DMO/DMOlog.old')
          os.system('sudo cp /home/pi/DMO/DMO.error /home/pi/DMO/DMOerror.old') 
          os.system('sudo shutdown -r now')
         
  print ('Mer ',positiestring[0:3],' Ven ',positiestring[3:6],' Aar ',positiestring[6:9],' Mar ',positiestring[9:12],' Jup ',positiestring[12:15],' Sat ',positiestring[15:18])

  # if there is a new position and we have got internet
  if str(positiestring) != str(positiestring_oud):   
      
    # first drive to magnet
    while (schakelaar == "open") and (not test_modus):
      kit.stepper1.onestep(direction=richting, style= stijl)
      if (io.digitalRead(19)):  
        schakelaar = "open"
      else:
        if teller > 200:
          schakelaar = "dicht"
      teller +=1
    sleep(1)  
   
    # calculation number of steps
    try:
       nieuwe_positie_planeet = int(positiestring[beginpos_string:eindpos_string])
    except:
       print ('FOUT in conversie van: ',  positiestring[beginpos_string:eindpos_string])
       nieuwe_positie_planeet = 1
    stappen_per_graad = totaal_stappen/360
    if (nieuwe_positie_planeet < magneet_positie) and (nieuwe_positie_planeet > 0):
       aantal_stappen_te_lopen = (magneet_positie - nieuwe_positie_planeet) * stappen_per_graad
    else:
       aantal_stappen_te_lopen =  ((360- nieuwe_positie_planeet)+ magneet_positie) * stappen_per_graad 
    
    print ('nieuwe_positie_planeet ' , nieuwe_positie_planeet)
    print ('stappen_per_graad ' , stappen_per_graad)
    print ('magneet_positie ' , magneet_positie)
    print ('aantal_stappen_te_lopen ' , aantal_stappen_te_lopen)      
   
    # drive to position
    teller = 1
    while (teller < aantal_stappen_te_lopen):
       if planeet_motor:
          kit.stepper1.onestep(direction=richting, style= stijl) 
       teller +=1    
    sleep (1)
   
  # wait 10 seconds to prevent overload of webserver
  sleep (10)
  totaalteller +=1
  if planeet_motor:
     kit.stepper1.release() 
      
  positiestring_oud = positiestring
  schakelaar = "open"
  teller = 1

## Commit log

2021-02-05 STL files
    [001 buitenkar SatJup versie2.stl, 001 buitenkar SatJup.stl, 002 buitenkar Mars.stl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]
2021-02-06 cleaned up STL files
    [001 buitenkar SatJup.stl, 003 VenusAarde versie 2.stl, 003 VenusAarde.stl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]
2021-02-06 update stl
    [005 wielhouder laag.stl, 006 wielhouder hoog.stl]
2021-02-06 update documentation
    [028 achterplaat mars.stl]
